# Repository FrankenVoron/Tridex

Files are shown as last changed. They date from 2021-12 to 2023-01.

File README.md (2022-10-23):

# Tridex

Screen_Shot_2022-10-16_at_11 43 59_AM

## Overview

The primary purpose of this IDEX (Independent Dual EXtrusion) printer is to enable dual material prints for soluble/removable supports (ie, ABS primary material + HIPS support material). Other methods of printing dual materials within a single toolhead (such as using a Y splitter, MMU, Palette, etc) have issues due to mixing/contamination within the nozzle which may cause poor layer adhesion. As well, these methods require fairly substantial purge blocks, which generally can be avoided with an IDEX design. 

If you need to prototype parts that have complex geometries (ie, prototyping parts that will be injection molded for mass production), this may be the printer for you! However, if you are designing parts with the final goal of being 3d printed, optimizing the design to be printed without supports will be more reliable, less expensive, and faster overall.

While this printer *may* eventually be "release worthy" with supporting documentation, please note **this is an advanced DIY 3d printer build.** This should not be your first DIY 3d printer, or your first Klipper 3d printer. There is a substantial amount of firmware configuration, macros, slicer setup, tuning, and calibration needed to get from a physically built printer to reliable multi material printer. 

## Specifications

Build Area: 

- Single Toolhead: 225x250x250mm
- Dual Toolhead: 205x250x250mm
- Mirrored/Duplication: Not currently supported with Klipper

Maximum Acceleration:

- Recommended 2000-4000 mm/s^2

This printer is based on the official Voron Trident release files: https://github.com/VoronDesign/Voron-Trident/releases

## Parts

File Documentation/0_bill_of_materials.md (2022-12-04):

# Tridex Bill of Materials

Items in **bold** are new items vs. a stock Trident build

Complete BOM in Progress (with Cost Delta): https://docs.google.com/spreadsheets/d/1dpyxq9-LeO-x1Jcv-8NuVuj9S6S3OHPWxxA0LcGV7Z0/edit?usp=sharing

Frame Calculator: https://docs.google.com/spreadsheets/d/1rIzYha_TP3Gi2qXVKMOwO2kwf7lOrjJWvsjmtj-F2lc/edit?usp=sharing

## Core Items:

- Trident Kit (250x250mm)
- Frame Extrusions:
  - 4 HFSB5-2020-500-LCP-RCP-AV360
  - **3 HFSB5-2020-470-TPW**
  - **1 HFSB5-2020-470-AH235-TPW**
  - **1 HFSB5-2020-470-AH235**
  - **1 HFSB5-2020-430**
  - 6 HFSB5-2020-370-TPW
  - **1 HFSB5-2020-340**
  - 1 HFSB5-2020-330-LTP
  - 1 HFSB5-2020-232-LTP
  - **2 DIN Rails (35mm W) - 470mm**
- **Stealthburner Kit (for 2nd toolhead)**
- **MGN12H 400mm with 2 MGN12H Carriages**
- **2 CAN Toolhead boards with CAN interface**
- **7+ Driver capable control board**
- **4 new Gates 2GT Belts**
  - **Y belt length = ~800mm * 2 belts**
  - **X belt length = ~1900mm * 2 belts**

## Front Idlers:

- **4 M5x50mm SHCS** 
- **2 M5x16 BHCS**
- 6 M5x10 BHCS
- 8 M5 2020 T-Nut
- **4 M5 Hexnut**
- 4 M5 Washer/Shims
- 2 M3x40 SHCS
- **2 M3x30 SHCS**
- 4 M3 Heatset Inserts
- 4 F695 Bearings
- **2 2GT 20T Toothed Idler Pulley (Gates or Generic)**

## XY Joints:

- 8 M5x40 SHCS
- 6 M5 Hexnuts
- 4 M5 Washers/Shims
- 4 M5 2020 T-Nut
- 4 F695 Bearings
- 2 2GT 20T Toothed Idler Pulley (Gates or Generic)
- **10 M3x20 SHCS**
- 4 M3x16 SHCS
- **2 M3 2020 T-Nut**
- **4 M3 Heatset Inserts**
- **High Temp Silicone Wiper**

## Drive Modules

- **4 NEMA14 Stepper Motors (V0.1 Style) - Options:**
  - LDO-35STH52-1504AH(VRN)
  - OMC 14HS20-1504S
  - LDO 35STH48-1684AH(VRN) 
  - (Ideally longer wiring harnesses than V0.1 to reach the bottom of the printer)
- 4 M5x30 BHCS
- **4 M5x16 BHCS**
- 14 M5x10 BHCS
- 16 M5 2020 T-Nuts
- 12 M5 Shims
- 12 F695 Bearings
- 8 M3x30 SHCS
- **6 M3x20 SHCS**
- **4 2GT 20T Pulleys (5mm Bore)**
- **2 Omron Microswitches**
- **4 M2x10 Self Tapping Screws**

## Panels

- Top/Back/Deck/Electronics/Door panels are widened by 100mm

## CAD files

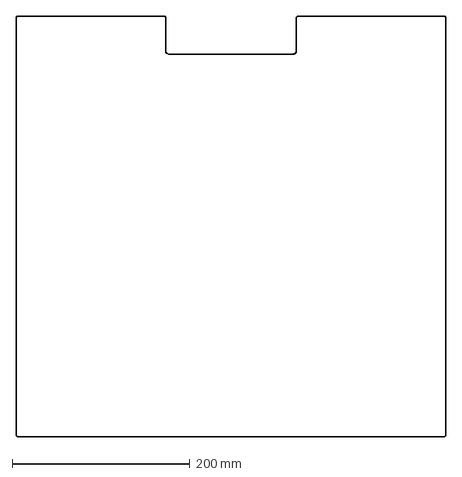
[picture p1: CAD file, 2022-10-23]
Drawings_DXF/350x250_rear.dxf
483.0 x 473.0 mm

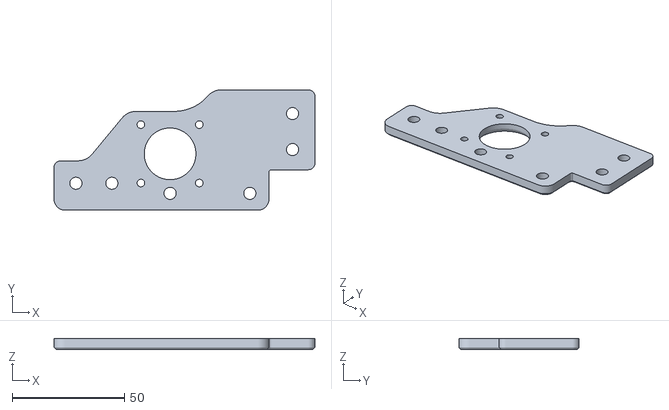
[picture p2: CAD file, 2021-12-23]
Gantry/AB_Drives/a_drive_frame_upper.stl
116.2 x 53.6 x 5.00

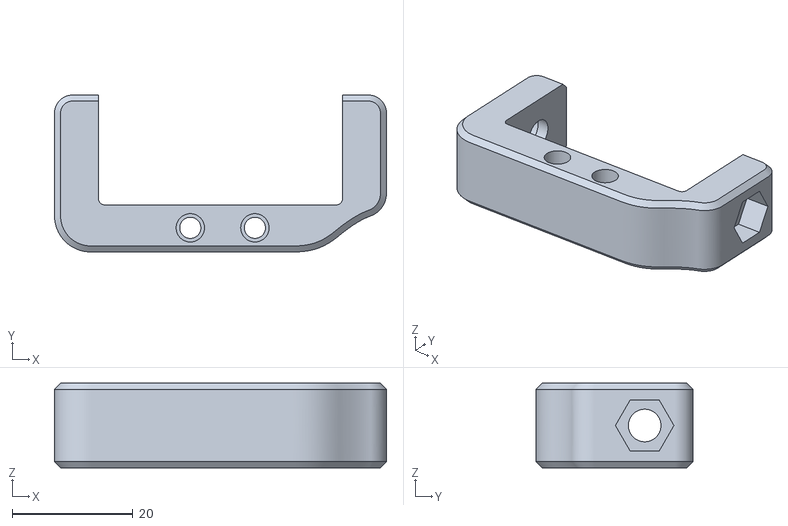
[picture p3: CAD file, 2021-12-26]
Gantry/Front_Idlers/Y_Left_tensioner_Stealth.stl
55.0 x 26.0 x 14.0

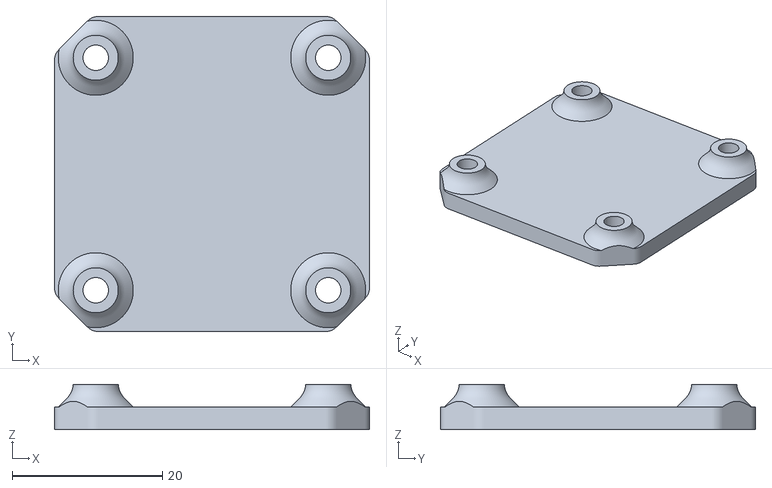
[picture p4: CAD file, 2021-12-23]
Gantry/X_Axis/Huvud_Mount_NEMA17.stl
42.0 x 42.0 x 6.00

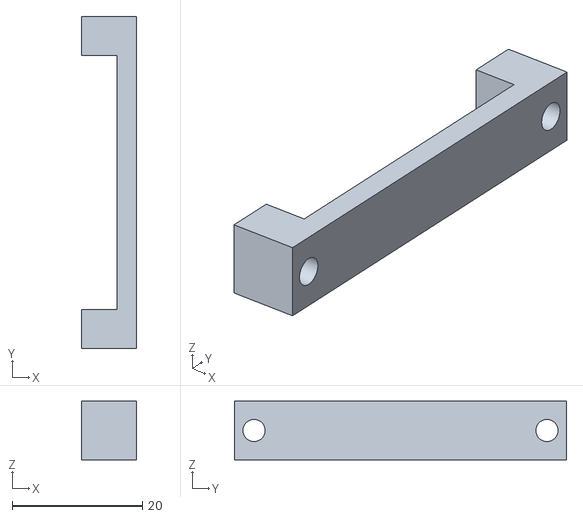
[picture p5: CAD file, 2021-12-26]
Gantry/X_Axis/Nozzle_Scrubber/Left_Brush_Clamp.stl
8.50 x 51.0 x 9.00

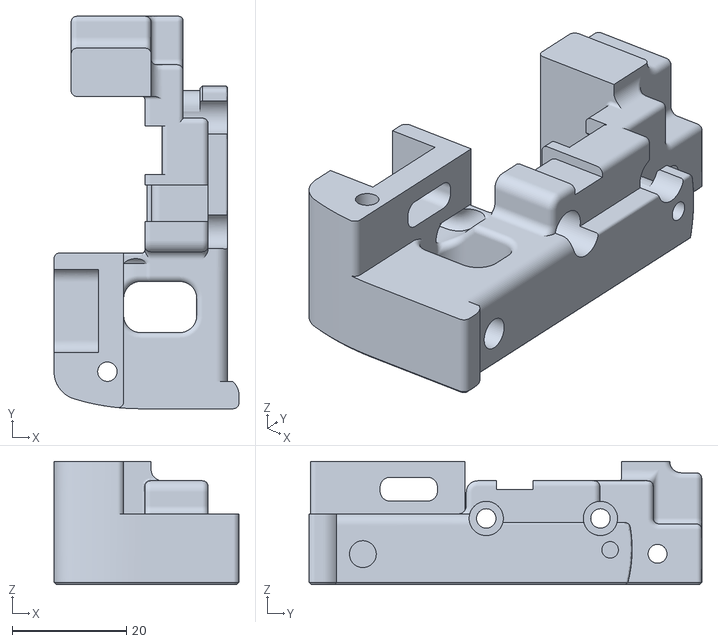
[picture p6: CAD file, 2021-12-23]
Gantry/X_Axis/X_Carriage/CW1 Version/x_carriage_frame_lower_right.stl
32.4 x 68.8 x 21.6

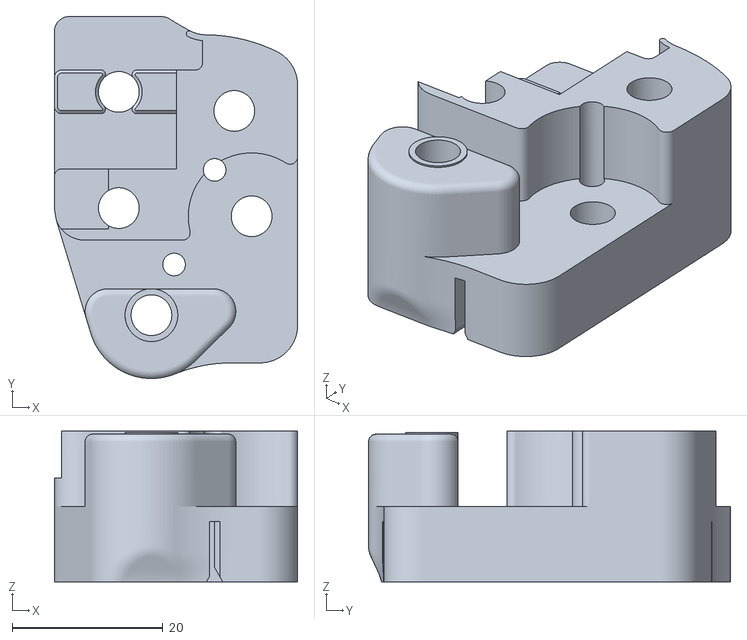
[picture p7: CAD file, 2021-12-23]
Gantry/X_Axis/XY_Joints/xy_joint_right_middle_MGN12.stl
32.3 x 48.0 x 20.0

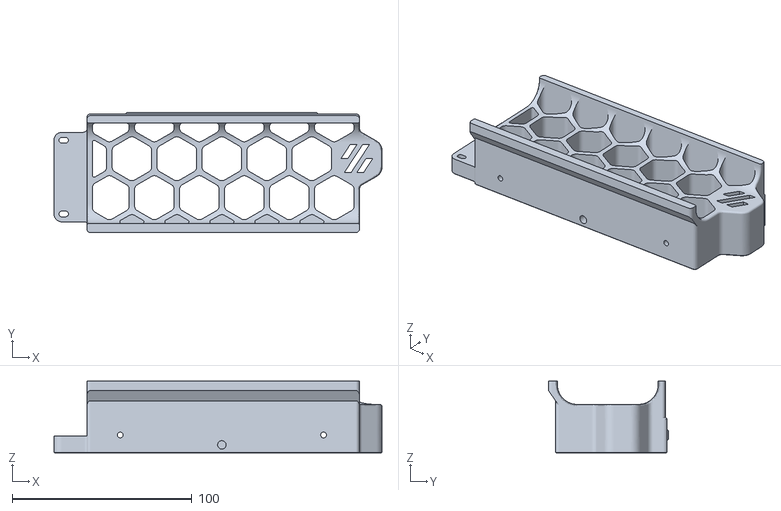
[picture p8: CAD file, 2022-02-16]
Skirts/front_skirt_a_350_deep.stl
182.3 x 66.8 x 40.0

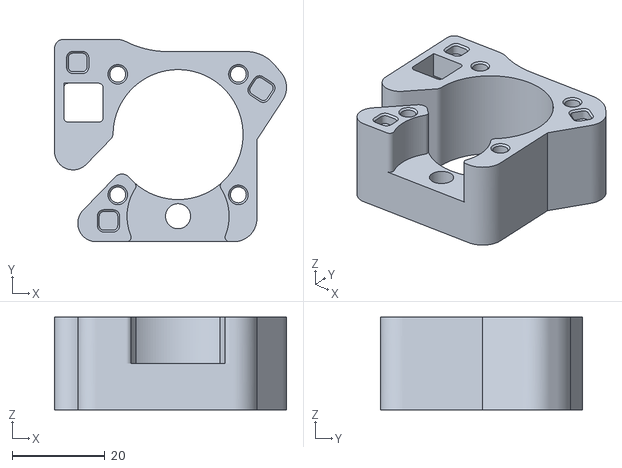
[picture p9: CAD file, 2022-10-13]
STLs/drive_modules/[a]_left_drive_mid.stl
50.0 x 43.7 x 20.0

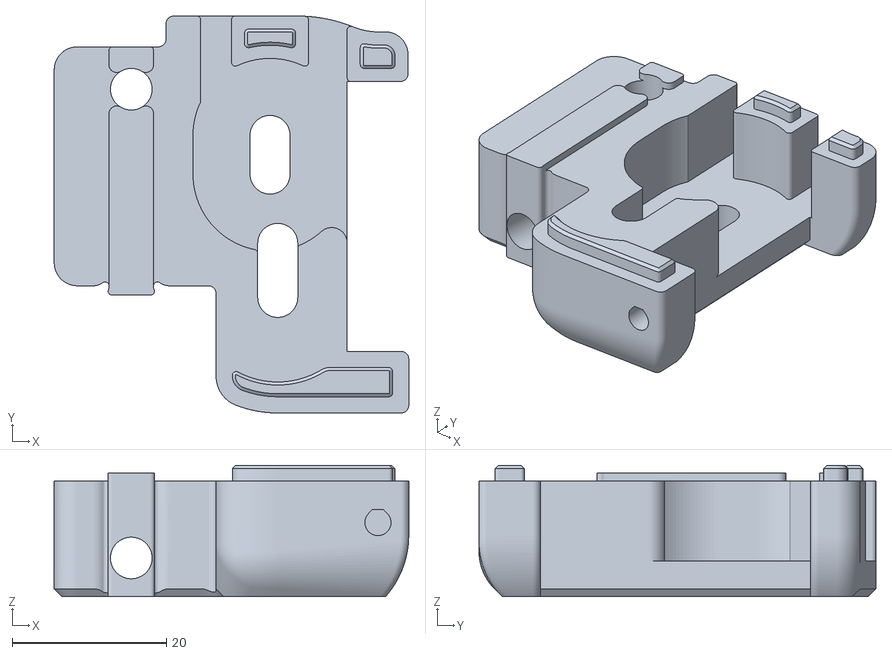
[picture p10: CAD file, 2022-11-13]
STLs/front_idler/idler_front_left_bottom.stl
46.0 x 51.5 x 17.0

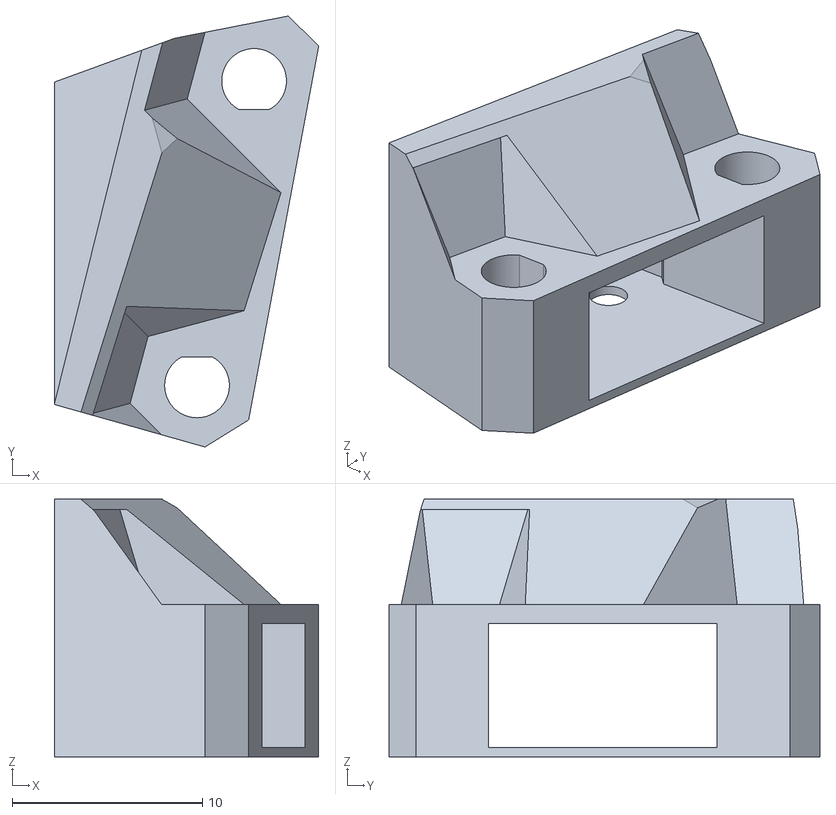
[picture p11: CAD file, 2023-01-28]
STLs/toolhead/Tridex_X_endstop.stl
13.9 x 22.6 x 13.5

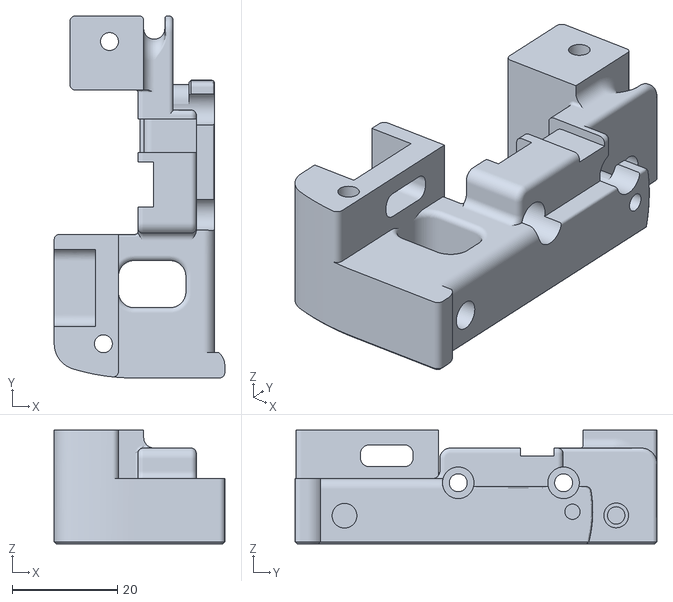
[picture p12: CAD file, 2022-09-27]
STLs/x_carriage_cw2/t0_x_carriage_frame_right.stl
32.4 x 68.8 x 21.6

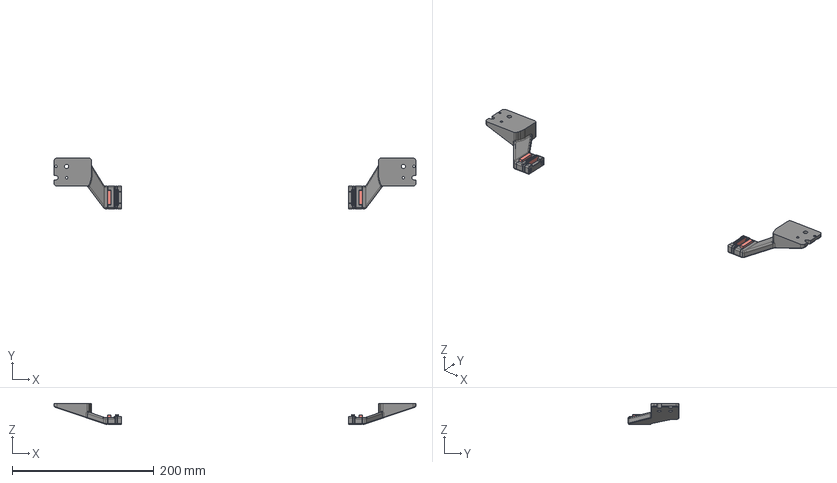
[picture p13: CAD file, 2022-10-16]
STLs/xy_joints/Tridex_XY_RC_Brush_Blocky v4.step
510.6 x 71.4 x 30.2 mm
M3x20 SHCS_91290A123 v1 x 4

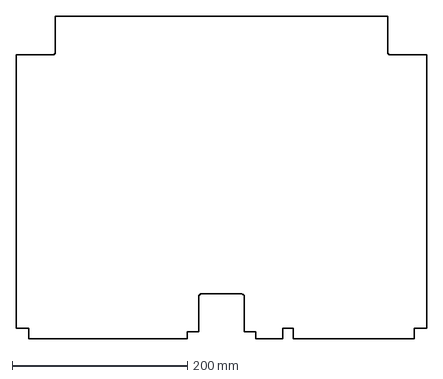
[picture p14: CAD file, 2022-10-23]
Drawings_DXF/350x250_deck.dxf
469.0 x 369.0 mm

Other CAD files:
Gantry/AB_Drives/a_y_motor.stl
Gantry/Front_Idlers/Y_Right_tensioner_Stealth.stl
Gantry/X_Axis/Nozzle_Scrubber/Right_Brush_Mount.stl
Gantry/X_Axis/X_Carriage/CW1 Version/x_carriage_frame_upper_left.stl
CAD/TrideX_Assembly_NozzleBrush v12.f3d
Drawings_DXF/350x250_bottom.dxf
Gantry/AB_Drives/[a]_a_drive_middle.stl
Gantry/AB_Drives/[a]_b_drive_middle.stl
Gantry/AB_Drives/a_drive_frame_lower.stl
Gantry/AB_Drives/b_drive_frame_lower.stl
Gantry/AB_Drives/b_drive_frame_upper.stl
Gantry/AB_Drives/b_y_motor.stl
Gantry/Front_Idlers/A_Tensioner_Stealth.stl
Gantry/Front_Idlers/B_Tensioner_Stealth.stl
Gantry/Front_Idlers/[a]_a_Tensioner.stl
Gantry/Front_Idlers/[a]_b_Tensioner.stl
Gantry/Front_Idlers/[a]_y_left_tensioner.stl
Gantry/Front_Idlers/[a]_y_right_tensioner.stl
Gantry/Front_Idlers/front_idler_a_lower.stl
Gantry/Front_Idlers/front_idler_a_middle.stl
Gantry/Front_Idlers/front_idler_a_upper.stl
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

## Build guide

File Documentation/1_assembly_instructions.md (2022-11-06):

# Assembly Guide for Tridex Gantry

This guide is meant to be a supplement to the standard Voron Trident and Voron Stealthburner/CW2 assembly manuals. It is not official, or final, but hopefully it will help you figure out the order of operations and make life a little bit simpler!

## Part 1: Basic Assembly

Follow the Trident manual, skipping the Front Idler, A/B Drive, and X Axis assembly. You may mount the entire Z assembly including the deck panel, bed, and electronics, and remake the CW2 and Stealthburner fan assemblies per the Stealthburner manual. Mount the Y MGN9 rails to the Y extrusions, but leave the screws loose so that they can slide slightly back and forth.

## Part 2: Drive Modules

Follow PDF instructions in this folder for drive module assembly. Once they are completed, install each drive module onto the gantry extrusions with M5x16 BHCS and M5x10 BHCS.

Fusion360_jOAN20uSyg

## Part 3: Front Idlers

Follow PDF instructions in this folder for front idler assembly. Once they are completed, install each front idler onto the gantry extrusions using M5x16 BHCS and M5x10 BHCS.

Fusion360_WQIAOHZXhy

After securing the front idlers and drive modules, install/slide the MGN9 Y rails backwards until they contact the drive modules. Use the MGN9 3d printed alignment tools to make sure the rail is centered, and secure the rail to the 2020 extrusion.

Fusion360_HXndMWOubw

There will be a gap on the front idlers. This is to allow variation in MGN9 length as well as make it easier to install/remove the drive modules/front idlers if needed in the future without completely removing the MGN9 rail. 

Fusion360_wkdUuxeDLE

## Part 4: XY Joints/Y Belts

Unlike standard Voron Trident XY joint assemblies, the Tridex XY joints must be assembled on the printer in stages. Mount the XY joint lowers to the MGN9 Y rails:

Fusion360_Avvm7I7o4f

Then, take a length of GT2 belt and feed it through the back of the front idler, loop around a GT2 idler, and then feed it through the other opening in the front idler:

Fusion360_W7kKqY3unr

Gently pull the belt out the back of the front idler. This will pull the GT2 idler into place.

Fusion360_r93V2uPN1i

Temporarily insert a M5x50 SHCS through the front idler (without the tensioner arm in place) to hold the GT2 pulley

Fusion360_IgsPVKHUWK

Take the belt closest to the 2020 Y extrusion, and feed it into the rear drive module. If you combine pressure and turning the GT2 pulley by hand, the belt will naturally follow the 3d printed surface and come out the other side. Make sure that belt is not twisted from the front toothed pulley all the way to the Y motor toothed pulley.

Fusion360_UmFg2cfLE5

Flip the left XY joint mid piece over so that you can see the toothed grooves 3d printed into the part.
Fusion360_vsk3gHWyFN
Fusion360_hWV8ZlinC8

For the "free" end of your GT2 belt, make sure it's trimmed cleanly at a 90 degree angle. Insert it into the part so that it overlaps the hole in the belt path. This hole is placed here so that you can push a small screwdriver or hex/allen key through it and push the belt out of the printed channel. 

Fusion360_kDndSNLoMT

With the long end of your GT2 belt, pull it tight and try to remove any obvious slack in the system. **Make sure that your front Y toothed pulley has the M5x50 SHCS through it to hold it into place, or you will cut your belt too short at this step!!**. Cut your belt so that it fits in the other slot in the printed part, similar to the red line in the image above. 

Flip the 3d printed part over, and snap it into the XY Joint Lower piece:

Fusion360_Hjc4LBXLTz

Make sure that the belts are oriented as follows. The "free" end of the Y belt will slide in a channel between the MGN9 carriage and the XY joint.

Fusion360_xVrUfiISvt

Manually pull the M5x50 SHCS screw forward in the Front Idler, and make sure the Y belt can be tensioned without too much front idler movement. If there is a lot of slack in the belt, consider trimming the belt one tooth shorter at a time until there's not much extra slack. As a tip--you can remove the M5x50 SHCS while installing the belt into the toothed slot to make it easier.

Once you are confident with the Y belt length, remove the Y belt, cut another Y belt of identical length, and then install both Y belts in the system. **Do not fully install the Y tensioner yet--just keep the M5x50 SHCS holding the GT2 idler**.

## Part 5: X Axis

Install the X axis MGN12 rail onto the 2020 extrusion. Install Tnuts as needed (2 M5 per side on top, 1 M3 per side on bottom) and screw the X axis to the partially assembled XY joint using a M3x20 from the bottom of the XY joint:

Fusion360_LfYs2FOs7U

Insert a M5x40 SHCS with washer/bearing/bearing/washer into the left XY joint:
Fusion360_kSubw5IJT0

Then install the XY joint upper on top. Insert the additional M5x40 SHCS, hexnuts, and GT2 20T idler:

Fusion360_KyqO03vBuD

On the right XY joint, install the XY joint upper with M5x40, washer/bearing/bearing/washer onto the lower/mid XY joint parts. Install the rest of the M5x40 screws, as well as the GT2 20T idler. 

Fusion360_0UUWuQsBGq

## Part 6: X Belts

In preparation for the X belts, install heatset inserts into the X carriages, and install the T0 X endstop into the left carriage. Do not install bolts through the X carriage yet--it is easier to install the belts with the X carriages as two separate halves.

Route an initial X belt by inserting the ends of the belts into the opening above the X pulley, fishing through the slots in the back of the drive module. 

Fusion360_TNfg9VQteW
Fusion360_Z8PnJcnRFt

The X belt routing is similar to a standard CoreXY belt routing, except upper belt attaches to the left X carriage (T1), and the lower belt attaches to the right X carriage (T1). 
Fusion360_s94B1QZMBw

Since the front tensioner Y accent pieces are not installed, it should be easier to route the X belts through the tensioner body. 

Fusion360_Zz1pREp1Aq

Once the belt is routed, temporarily install an X carriage and pull the X axis flush to the front of the printer, to make sure there is enough belt length. You can leave an inch or two extra belt sticking out of the X carriage if needed

Cut the X belt, and then remove, and cut another X belt exactly the same length. Install both belts, making sure that both have the same amount of extra belt length extending from the X carriages. With this complete, install the M3x30 bolts through the X carriages to make sure both halves are fully secured. 

Remove the M5x50 SHCS from the front Y idler pulleys, and finally install the Y tensioners and tensioning screws
Fusion360_ggaEBeqQwN

If you have difficulty aligning the 20T toothed idler with the M5x50 screw, use an allen key or small screwdriver to push it backwards from the bottom while you insert the M5x50 back in from the top.

## Part 7: Tensioning and Alignment

With all belts installed, double check all belt routing to make sure belts are fully seated on their bearings/pulleys. 

Push the X axis backwards so it's about 3/4 of the way to the back of the printer. Pluck the Y belts (between the XY joints and front idlers) and tension them until there is a clear low bass tone, even on both sides. My printer is currently around 60Hz at about Y=200mm, but this is not scientific. Pluck the X belts and tension them so they match the same tone. Push the X axis backwards and check to see if both Y endstops trigger at the same time--if they do not, slightly tweak the X belt tension until they do. If they don't reliably trigger, install the "Y Endstop Bumpers" (not yet designed) to improve Y endstop performance. 

Check all belt tensions again once both Y endstops are triggering at the same time. If the belt tensions are significantly different between X1/X2, loosen the screws connecting the X axis extrusion to the XY joints, recheck Y endstop triggering/belts, and once belt tension is the same across all belts and the Y endstops trigger at the same time, tighten the X axis 2020/XY joints for a final time. Check all structural bolts through the gantry to make sure they are moderately tight. DO NOT OVERTIGHTEN, just snug: M5x30 BHCS on Drive Modules (idler pulley axles), M5x40 SHCS holding idler pulleys on XY joints, M5x50 SHCS on Front Idler tensioners.

Later on, recheck belt tensions once the printer has homed XY and stepper motors are engaged.

## Part 8: Nozzle Wiper Assembly

Take the nozzle wiper components and insert two heatsets into the ends of each nozzle wiper body. Cut pieces of silicone wiper (based on template) and insert into the slots. Secure silicone pieces with M3x20 SHCS to the end of the wiper body. To mount the wiper assembly to the bottom of the XY joint, note that two of the XY Joint Lower to MGN9 Y rail screws have passthroughs in the nozzle wiper body, and two will be used to mount. Remove the two M3x16 SHCS screws (diagonally) where the nozzle wiper will mount to the XY Joint Lower, and put M3x20 SHCS through the nozzle wiper body, thorugh the XY Joint Lower, and into the MGN9 carriage. Tighten securely, and repeat with both sides.

## Part 9: Toolhead Assembly

Assemble two CW2 modules per the standard CW2 instructions. Mount your choice of CAN control board to the back/sides based on the model. NEMA14 sized CAN boards can be mounted with M3 brass standoffs off the NEMA14 motor, HUVUDs/NEMA17 can be mounted with an arm that replaces the cable chain mount. Stealthburner style CAN boards can be installed integrated into the body of the Stealthburner/CW2. 

For the T0 toolhead (left), print the specific toolhead_rear component in the Tridex repo along with the standard toolhead_front from the stealthburner repo. This modified toolhead_rear has a bumper extension that will allow T1 to home off of it. Note--this toolhead_rear part requires supports at this time. 



For the T1 toolhead (right), print the standard toolhead_front and toolhead_rear from the Stealthburner repo, along with the custom X endstop mount from the Tridex repo. Mount a microswitch with lever into the X endstop mount, with wire leads extending through the toolhead_rear mount behind the hotend heatsink, where the wires will join the rest of the hotend thermistor/heater wires to travel up to CW2. 



Mount the X endstop mount to the toolhead body with M3 screws into the heatset inserts in the toolhead body.







Assemble the Stealthburner fan assembly per the standard instructions. Double check the X carriage is sitting flush/properly with the MGN12H rail and all screws are tight--if it is not, it will create large offsets between the toolheads. Mount the CW2, Toolhead, and Stealthburner onto the X carriage, and tighten securely. Make sure any extra 2GT belt does not get pinched between the toolhead body and the X carriage, since this will create large offsets.

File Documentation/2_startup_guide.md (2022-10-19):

# Initial Startup Guide

This guide is heavily inspired by Klipper's Configuration Check guide: https://www.klipper3d.org/Config_checks.html

## 1. Klipper Setup

Flash MainsailOS or FluiddPi to your Raspberry Pi micro SD card, and configure your microcontroller and CAN interfaces. There are a variety of different resources available that may be helpful, but it is expected that you will be comfortable flashing/configuring the device that you choose!

- [MainsailOS](https://github.com/mainsail-crew/MainsailOS/tags)
- [FluiddPi](https://github.com/fluidd-core/FluiddPI/tags)
- [Klipper Mainsail CAN Setup Guide](https://www.youtube.com/watch?v=XkcxSQhRR3I)
- [CanBoot Flashing Guide](https://youtu.be/YrF99Sff9g8)
- [BTT EBB V1.0 CAN Setup Guide](https://youtu.be/_FELCN8CbWA)

## 2. Configuration

### Endstop Checks

Save the firmware configuration files from the Tridex Github to your printer, and edit them to match your control boards and printer specification. Once Klipper starts successfully without throwing errors, verify each of the endstops to make sure they function as expected by manually triggering the endstop with your finger or a tool. The status can be checked in the "Machine" page of Mainsail by refreshing the endstop status section.

- Endstop X (left toolhead X endstop)
- Endstop Dual_Carriage (right toolhead X endstop)
- Endstop Y (left Y endstop)
- Endstop Y1 (right Y endstop)
- Endstop Z (Z nozzle pin)
- Probe (Omron probe or Klicky, etc)

Once each endstop is configured so that it reads `Triggered` when pressed, and `Open` when not pressed, go ahead and push the X axis towards the back of the printer and make sure that both Y endstops trigger off of the X axis. If only one can trigger, tighten or loosen one of the X belt tensioners until both trigger approximately simultaneously. Also, verify that the T0 (left) toolhead X endstop can physically trigger off of the left XY joint, and that the T1 (right) toolhead X endstop can trigger off of the T0 (left) toolhead. 

### Stepper Motors

Next, let's talk about stepper motors checks! Similar to single toolhead Voron printers, the origin (X=0, Y=0) is located at the front left corner of the bed, with positive X traveling to the right, and positive Y movement traveling to the back. For starters, we need to make sure all of the motors are connected to the right connectors and are moving the correct directions. For this, we will use  `STEPPER_BUZZ STEPPER=[stepper name]`. This command will move the stepper back and forth--the first movement after sending the command will be in the "+" axis direction, and then "-". 

- `STEPPER_BUZZ STEPPER=stepper_x` - T0 (left toolhead) should move right (+), then left (-)
- `STEPPER_BUZZ STEPPER=dual_carriage` - T1 (right toolhead) should move right (+) then left (-)
- `STEPPER_BUZZ STEPPER=stepper_y` - left Y motor should move back (+) and then to the front (-)
- `STEPPER_BUZZ STEPPER=stepper_y1` - right Y motor should move back (+) and then front (-)
- `STEPPER_BUZZ STEPPER=stepper_z`- front left Z motor should move down (+) and then up (-)
- `STEPPER_BUZZ STEPPER=stepper_z1`- back Z motor should move down (+) and then up (-)
- `STEPPER_BUZZ STEPPER=stepper_z2`- front right Z motor should move down (+) and then up (-)

### Homing

Next, we need to check the homing sequence. The order of homing is different with a Tridex than with a Trident. An overview of the order is as follows:

1. Home Y to Y=max (back of printer)
2. Home T0 (left toolhead) to X=min (left of printer)
3. Home T1 (right toolhead) to T0 (left of printer)
4. Move T1/Park T1
5. Move T0 to Z endstop pin location
6. Home Z

The default printer configuration file already has homing set up properly for you, however, this configuration file may be updated in the future to be more universal and user friendly. For now, follow these steps **and be sure to have access to the "Emergency Stop" button in Mainsail/Fluidd**:

1. Use macro `IDEX_HOME_Y` (visible on Mainsail dashboard). The printer should move the X axis backwards until both Y endstops are triggered, and then move forward approximately 35mm. **If it moves to the front of the printer at first and doesn't stop, hit the Emergency Stop button! If the Y motors move in opposite directions, hit the Emergency Stop button!** 

If either of these cases occurs--double check your STEPPER_BUZZ commands and invert the direction pin of the stepper motor that is not traveling in the correct direction. Also, double check your `position_endstop`--it should be set equal to position_max. If it is set to something else (like position_min)--the printer will home in the incorrec direction. 

2. Once you have successfully homed Y, use macro `IDEX_HOME_X`. The printer should move the left toolhead (T0, controlled by stepper_x) to the left until it triggers the T0 x endstop, and then it should move the right toolhead (T1, controlled by dual_carriage) to the left until it triggers the T1 x endstop. Then, it should move the T1 toolhead to the right to about the middle of the printer, and then move it to the parked position close to the right of the X axis. T0 should become active at this point, and move to about the center of the printer. **If either toolhead doesn't travel in the correct direction, or crashes, press the Emergency Stop Button immediately!** 

The initial printer.cfg in the Tridex repository should properly define the `position_endstop` for both `stepper_x` and `dual_carriage`, but if you have issues with homing, double check both the `STEPPER_BUZZ` directions and toolheads as well as the position endstop for both. `[stepper_x]` should have a `position_min` and `position_endstop` of approximately -50, and `[dual_carriage]`should have `position_min` and `position_endstop` of approximately 22. 

3. Once both X and Y have homed successfully, (by running `IDEX_HOME_Y` and then `IDEX_HOME_X`), make sure T0 is active (press the T0 button in Mainsail), and move the toolhead using Mainsail until the nozzle is above the Z endstop pin. Record these coordinates (X and Y) and update your [homing_override] section so that the toolhead goes to this point prior to homing Z. (More documentation needs to be added for this step). Your z pin location should be somewhere close to X = 145-150mm and Y = 250-255mm for a standard 250x250mm Tridex build. 
4. Once you have updated your configuration, saved it, and restarted klipper, now is the exciting point! Press the "Home All" button in Mainsail. The printer should home Y, home X, and then move T0 to the Z endstop pin location and home. **Be sure to be ready to press the Emergency Stop button!** 

Even if the nozzle touches the Z endstop pin successfully, double check the location again and make sure that the nozzle is as close to the center of the Z endstop pin as possible. With this final adjustment, save the configuration, restart the printer, and home again!

5. Finally, we need to verify that the probe works as expected! If you are using an inductive probe, make sure that the probe triggers off of a piece of metal and the bed by checking the endstop status. Then, run a Z_TILT_ADJUST (or "Z-TILT" in Mainsail) to level the bed. Finish by running a final G28 to home Z again off of the Z pin. 

Congratulations! You've successfully homed your Tridex printer!

### Heaters and Fans

Follow the standard [Klipper Configuration Checks](https://www.klipper3d.org/Config_checks.html) guide to test each of your hotend fans, hotend heaters, part cooling fans, and bed heater. PID calibrate each heater individually, saving the configuration after each tune.

### Extruder

With your hotend heated, try extruding some filament through each toolhead. If the extruder is going in the wrong direction (retracting instead of feeding filament), invert the direction pin for that given extruder. Press the "T0" or "T1" buttons to switch between toolheads to test each one. Finally, calibrate your extruder by extruding 100mm of filament and verifying that 100mm of filament is fed through the extruder. It is critical that both extruders are functionally extruding the same amount of filament!

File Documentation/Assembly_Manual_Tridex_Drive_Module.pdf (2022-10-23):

Y ENDSTOP MOUNTING | WWW.VORONDESIGN.COM

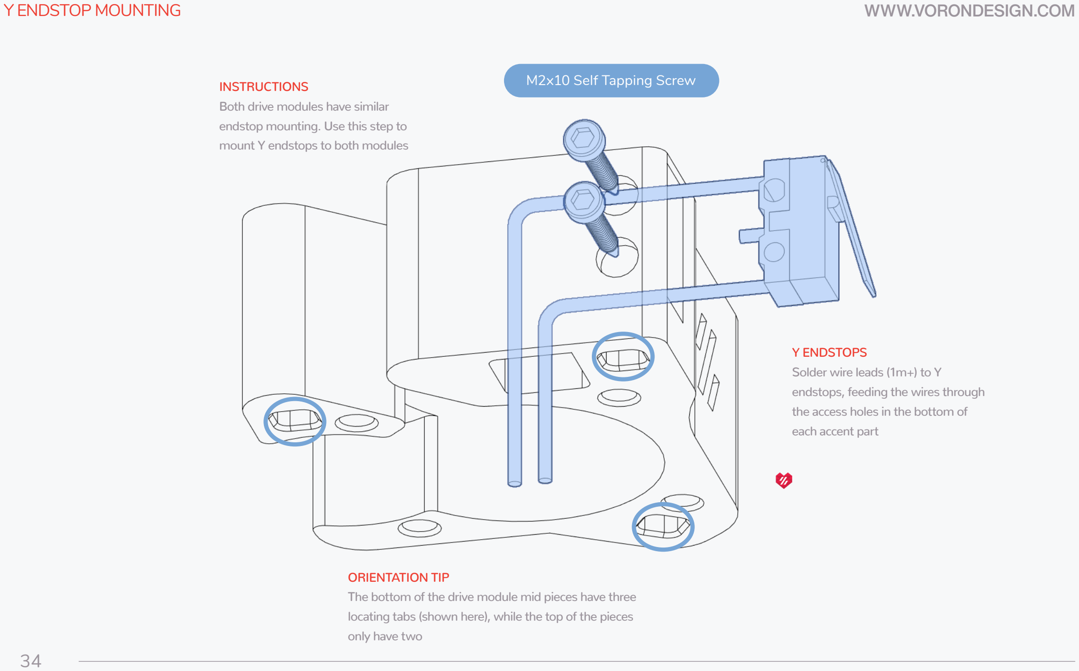
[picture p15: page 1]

34

Y ENDSTOPS
Solder wire leads (1m+) to Y endstops, feeding the wires through the access holes in the bottom of each accent part

INSTRUCTIONS
Both drive modules have similar endstop mounting. Use this step to mount Y endstops to both modules

ORIENTATION TIP
The bottom of the drive module mid pieces have three locating tabs (shown here), while the top of the pieces only have two

M2x10 Self Tapping Screw

LEFT DRIVE MODULE | WWW.VORONDESIGN.COM

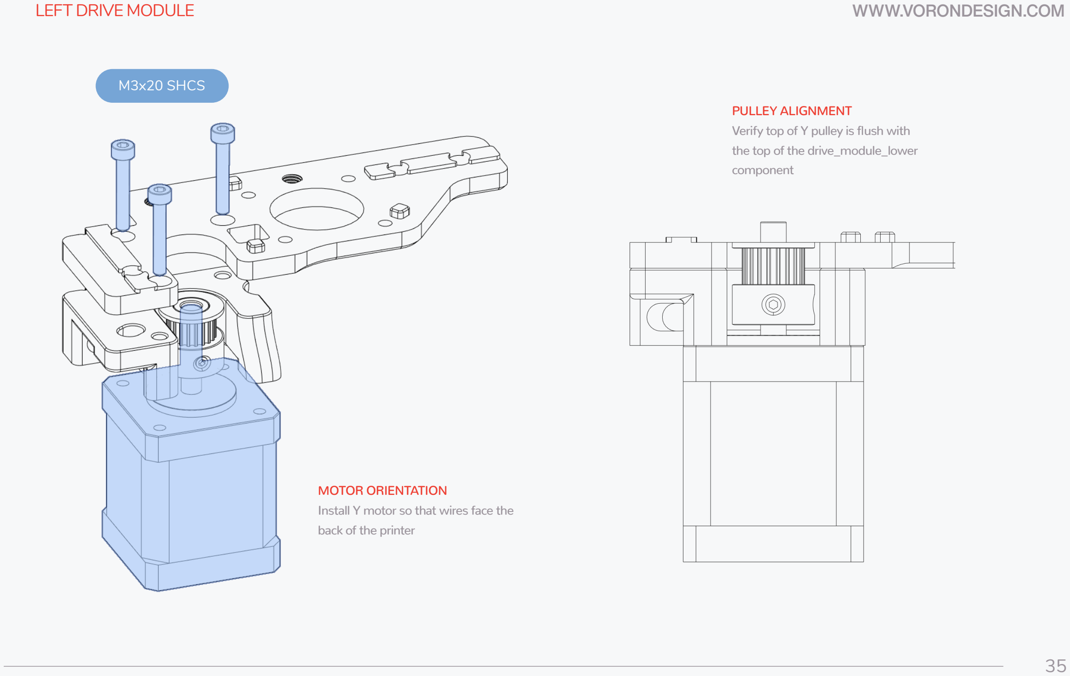
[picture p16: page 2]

35

M3x20 SHCS

MOTOR ORIENTATION
Install Y motor so that wires face the back of the printer

PULLEY ALIGNMENT
Verify top of Y pulley is flush with the top of the drive_module_lower component

### WWW.VORONDESIGN.COM

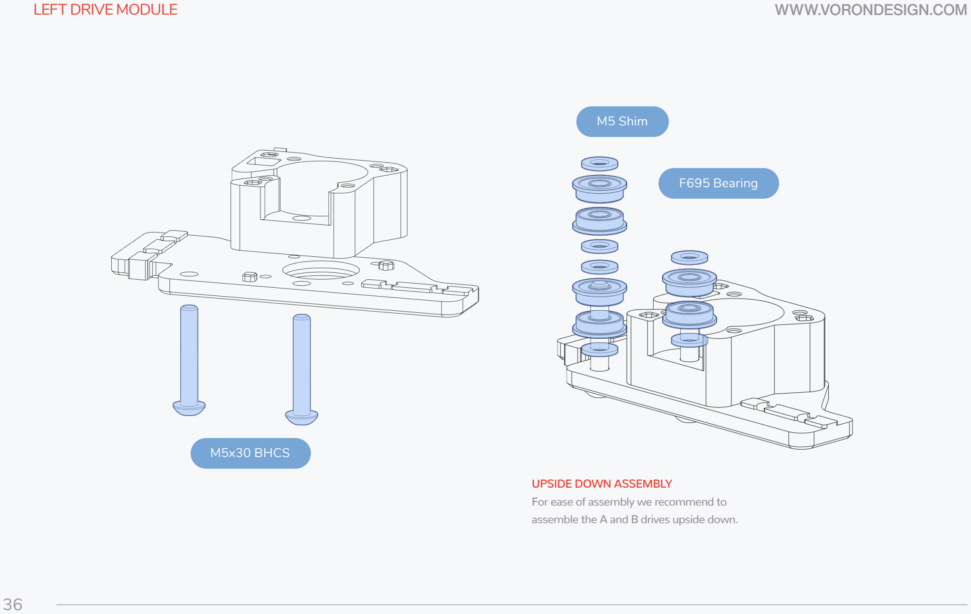
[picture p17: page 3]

36

M5 Shim

F695 Bearing

LEFT DRIVE MODULE

UPSIDE DOWN ASSEMBLY
For ease of assembly we recommend to assemble the A and B drives upside down.

M5x30 BHCS

LEFT DRIVE MODULE | WWW.VORONDESIGN.COM

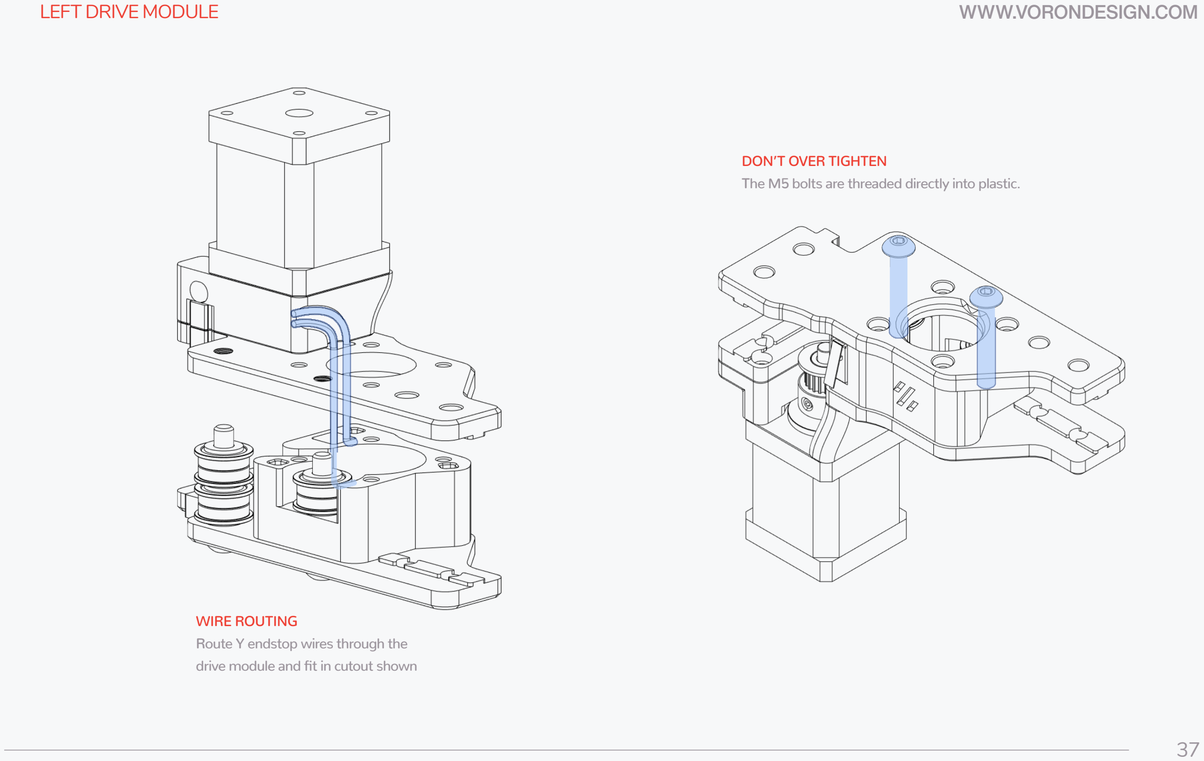
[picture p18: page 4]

37

WIRE ROUTING
Route Y endstop wires through the drive module and fit in cutout shown

DON’T OVER TIGHTEN
The M5 bolts are threaded directly into plastic.

LEFT DRIVE MODULE | WWW.VORONDESIGN.COM

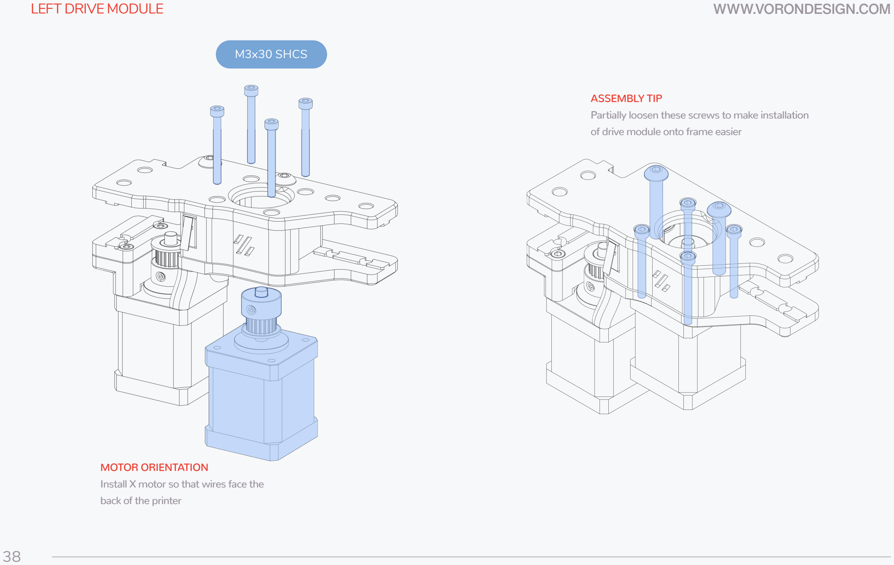
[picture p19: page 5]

38

ASSEMBLY TIP
Partially loosen these screws to make installation of drive module onto frame easier

M3x30 SHCS

MOTOR ORIENTATION
Install X motor so that wires face the back of the printer

RIGHT DRIVE MODULE | WWW.VORONDESIGN.COM

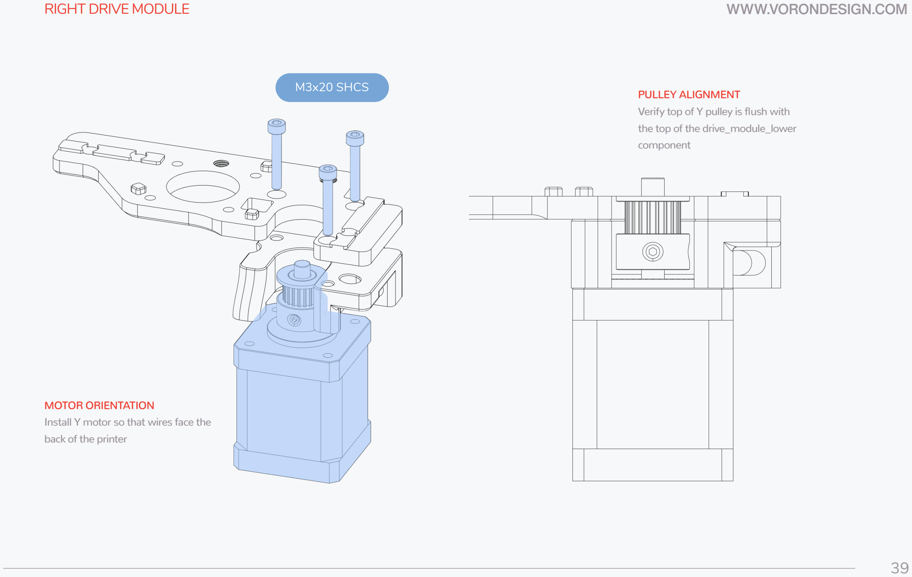
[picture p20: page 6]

39

M3x20 SHCS

MOTOR ORIENTATION
Install Y motor so that wires face the back of the printer

PULLEY ALIGNMENT
Verify top of Y pulley is flush with the top of the drive_module_lower component

RIGHT DRIVE MODULE | WWW.VORONDESIGN.COM

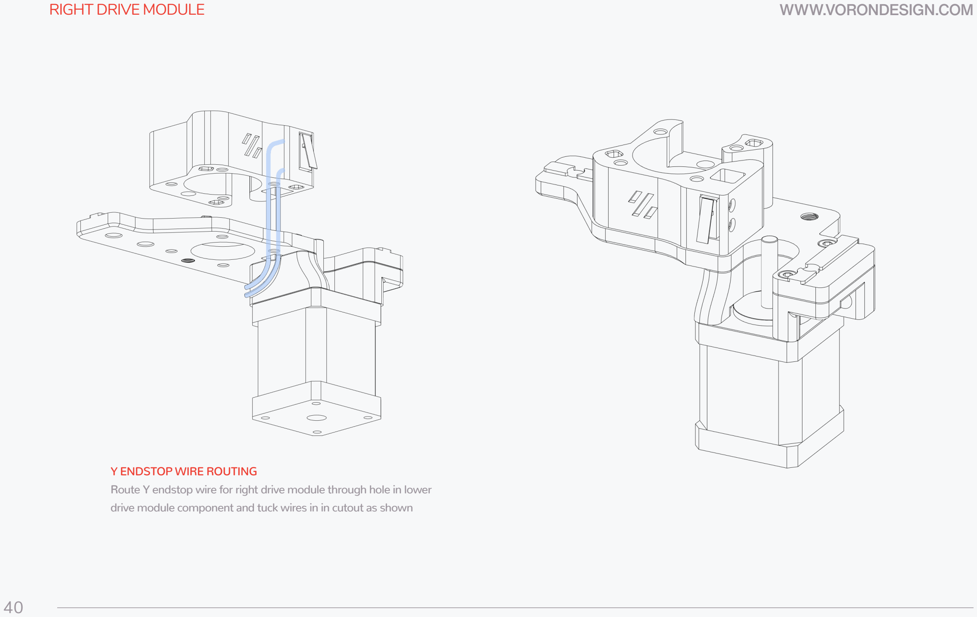
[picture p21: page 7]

40

Y ENDSTOP WIRE ROUTING
Route Y endstop wire for right drive module through hole in lower drive module component and tuck wires in in cutout as shown

### WWW.VORONDESIGN.COM

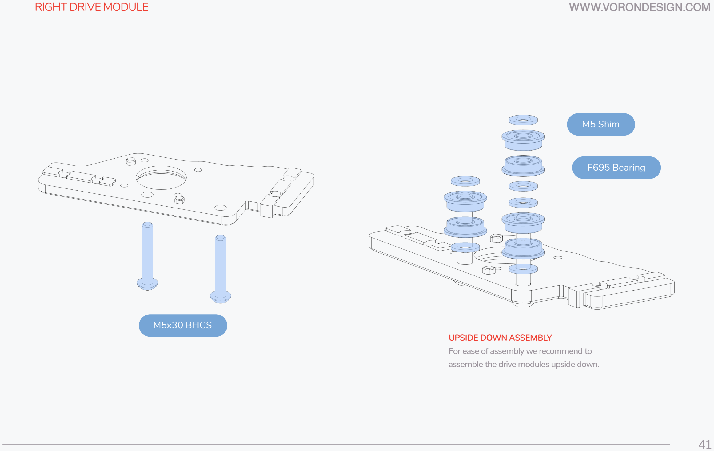
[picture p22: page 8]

41

M5 Shim

F695 Bearing

RIGHT DRIVE MODULE

UPSIDE DOWN ASSEMBLY
For ease of assembly we recommend to assemble the drive modules upside down.

M5x30 BHCS

RIGHT DRIVE MODULE | WWW.VORONDESIGN.COM

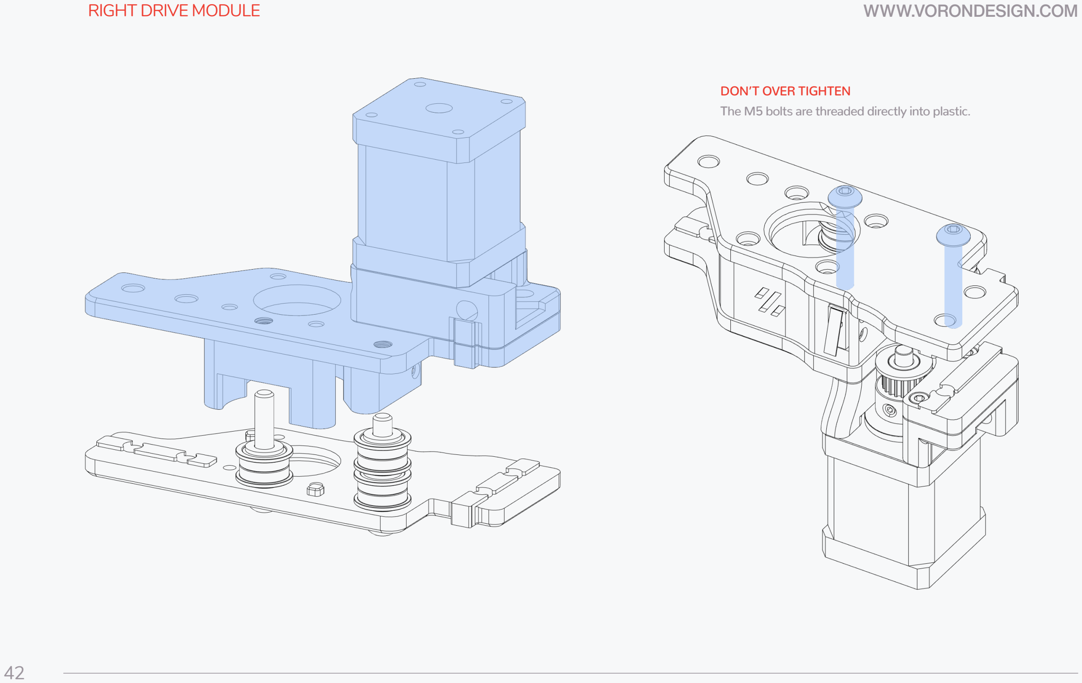
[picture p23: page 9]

42

DON’T OVER TIGHTEN
The M5 bolts are threaded directly into plastic.

RIGHT DRIVE MODULE | WWW.VORONDESIGN.COM

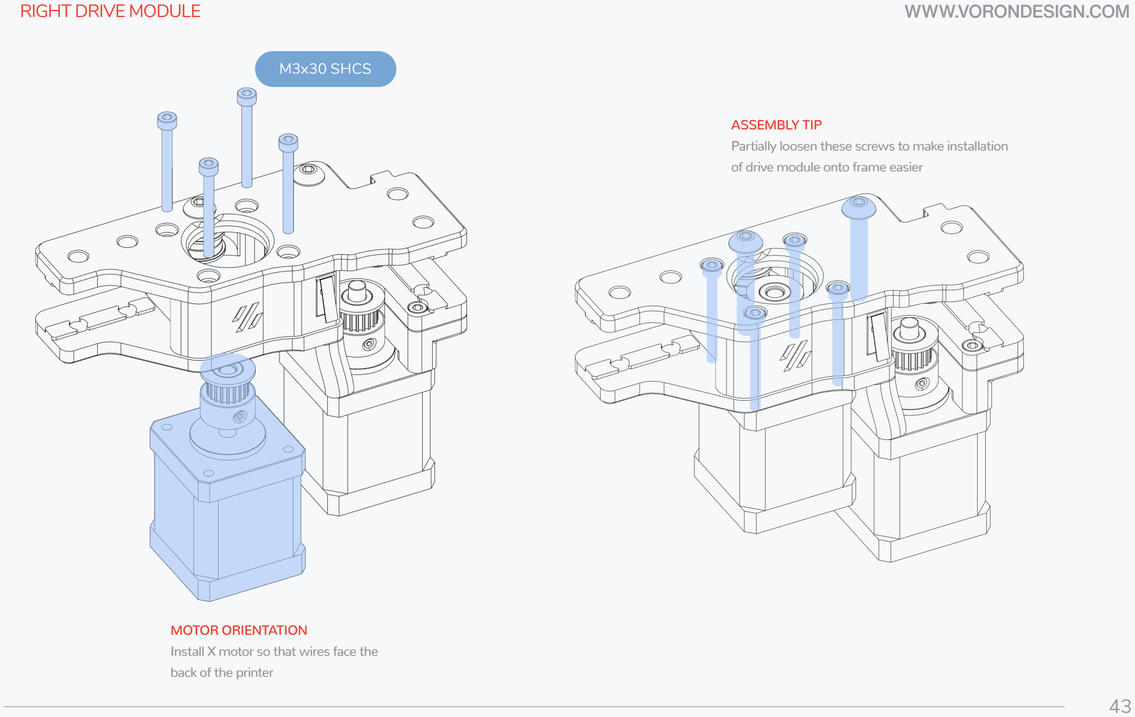
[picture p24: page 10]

43

ASSEMBLY TIP
Partially loosen these screws to make installation of drive module onto frame easier

M3x30 SHCS

MOTOR ORIENTATION
Install X motor so that wires face the back of the printer

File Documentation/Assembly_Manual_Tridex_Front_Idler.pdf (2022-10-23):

COMPONENT PREP | WWW.VORONDESIGN.COM

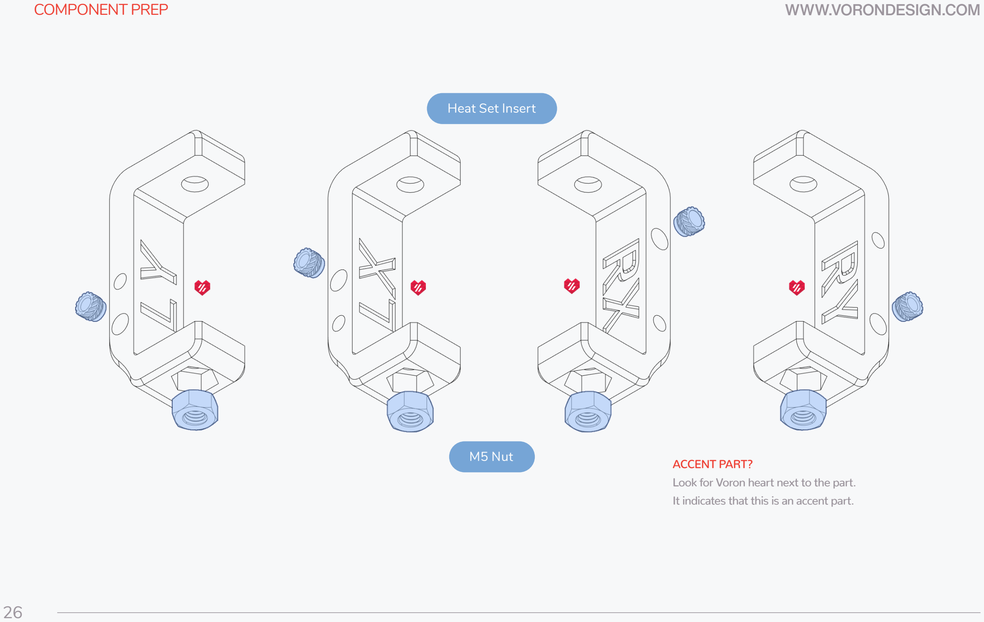
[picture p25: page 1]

26

M5 Nut

Heat Set Insert

ACCENT PART?
Look for Voron heart next to the part. It indicates that this is an accent part.

LEFT IDLER | WWW.VORONDESIGN.COM

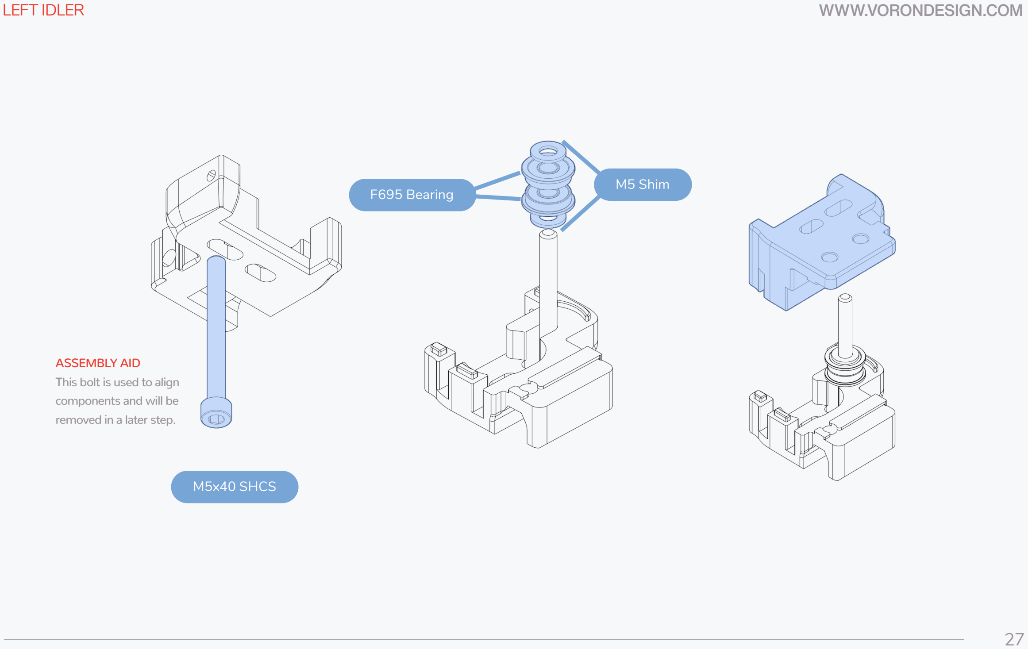
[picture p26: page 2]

27

M5x40 SHCS

M5 Shim
F695 Bearing

ASSEMBLY AID
This bolt is used to align components and will be
removed in a later step.

LEFT IDLER | WWW.VORONDESIGN.COM

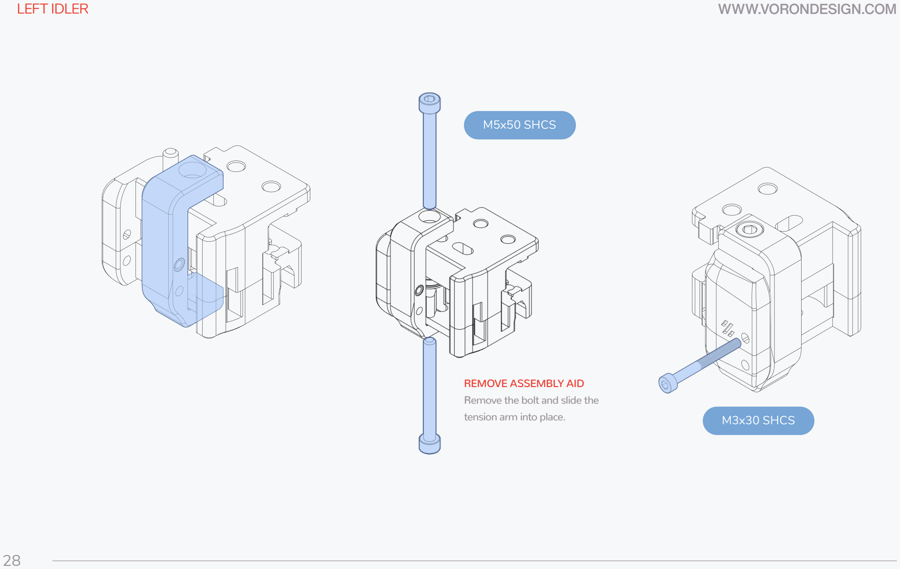
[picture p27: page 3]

28

M5x50 SHCS

M3x30 SHCS

REMOVE ASSEMBLY AID
Remove the bolt and slide the tension arm into place.

RIGHT IDLER | WWW.VORONDESIGN.COM

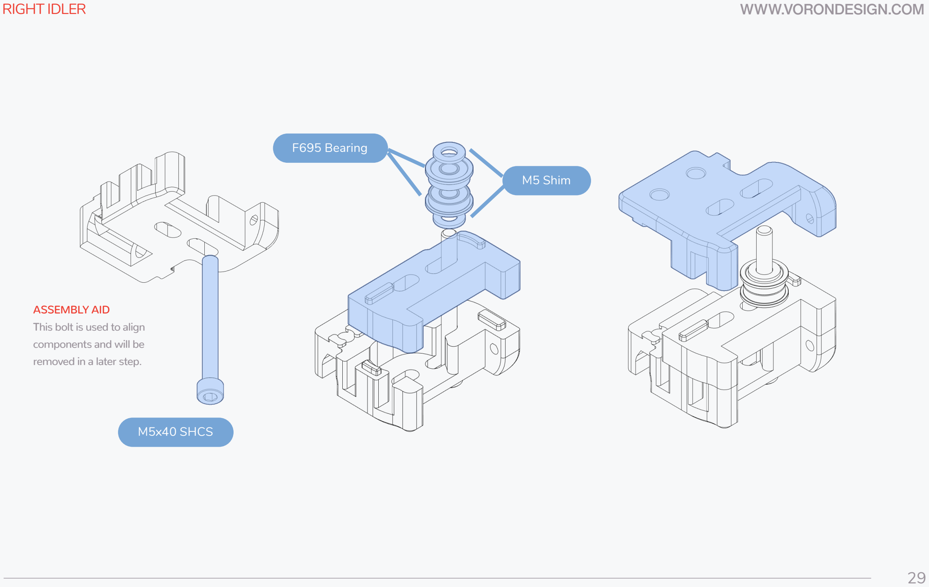
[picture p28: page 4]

29

M5x40 SHCS

M5 Shim

F695 Bearing

ASSEMBLY AID
This bolt is used to align components and will be
removed in a later step.

RIGHT IDLER | WWW.VORONDESIGN.COM

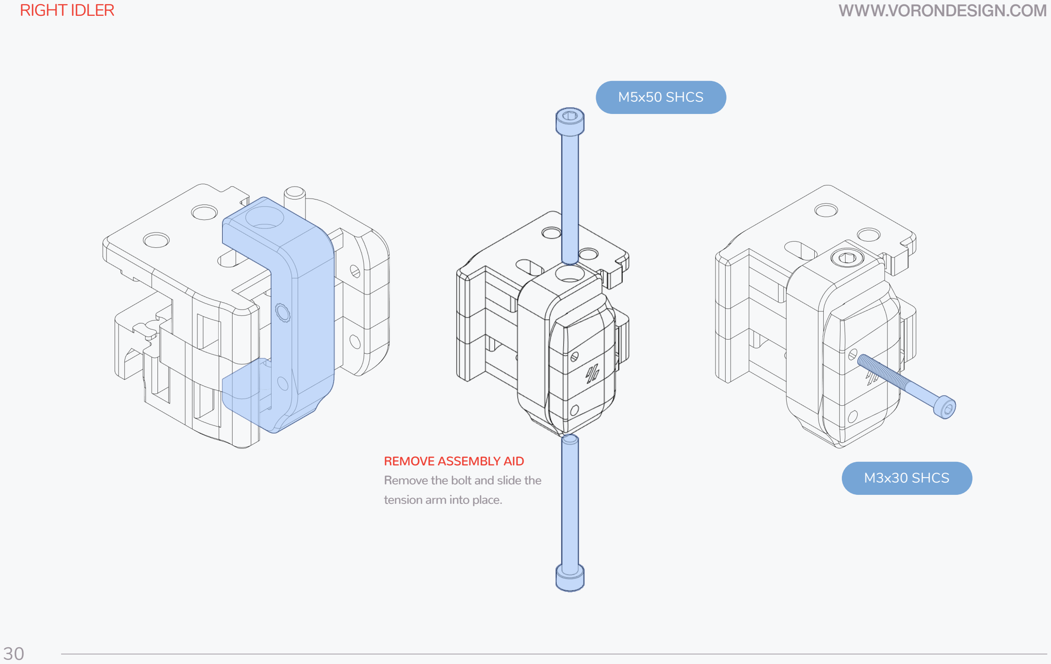
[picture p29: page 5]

30

M5x50 SHCS

M3x30 SHCS

REMOVE ASSEMBLY AID
Remove the bolt and slide the tension arm into place.

FRONT IDLERS | WWW.VORONDESIGN.COM

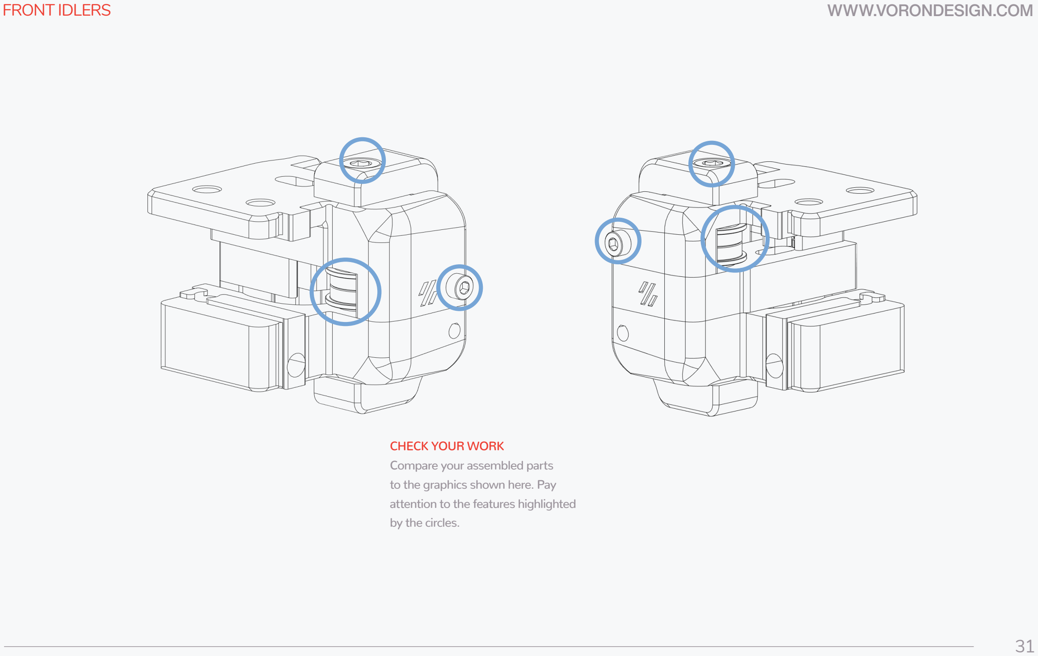
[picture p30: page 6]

31

CHECK YOUR WORK
Compare your assembled parts to the graphics shown here. Pay attention to the features highlighted by the circles.

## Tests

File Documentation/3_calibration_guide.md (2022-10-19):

# Calibration Guide

This guide is a work in progress, and is a collection of different tuning steps that may not be complete or have the supporting configuration parameters. This guide assumes you have followed the previous getting started guide and your printer homes and extrudes filament!

## Rough Offset Calibration

For an IDEX printer, we have 3 offsets that we need to calibrate--X, Y, and Z! Check your IDEX_mode.cfg file and verify that all of your offset variables are set to 0 (variable_offset_x, variable_offset_y, and variable_offset_z). 

First off, it's important that your T0 (left, primary) toolhead is printing well and has a good first layer Z position. Using a hot bed and extruder, move the T0 nozzle to the center of the bed and lower the nozzle until it barely touches a sheet of paper as the paper is moved back and forth. This height should be approximately Z = 0.1mm. Adjust the `[stepper_z]` `position_endstop`, save, restart Klipper, and test until this is true.

Once your T0 nozzle is touching the sheet of paper at 0.1mm, raise the toolhead a few millimeters, switch to T1, and begin lowering the T1 nozzle until it touches the sheet of paper. Record the value--if T1 is touching at 0.17mm and T0 is touching at 0.1mm, the `variable_offset_z` will be T1 - T0 = 0.17 - 0.1 = 0.07mm. Update your IDEX_mode.cfg file and restart Klipper.

Next, let's tune the variable_offset_x! After homing the printer, find an object (such as a block) and place it on the print bed, raise or lower the bed height as necessary so that the nozzle is within a few millimeters of the block. Move the block around until one of the edges is aligned with the center of the T0 nozzle. Record the X position of T0 at this point, then switch to T1, and move the toolhead back and forth in X using the commands in Mainsail until the nozzle is positioned the same as the T0 nozzle was. Record the T1 position, and then calculate the new variable_offset_x as T1_x - T0_x = value. Update your IDEX_mode_cfg file and restart klipper! (Note--if this offset value is very large, you can choose to update the dual_carriage position_endstop instead so that the offset is small)

Finally, tune variable_offset_y. Use the same setup as with X, except adjust the toolheads in Y instead of X! 

These initial calibration values are rough approximate values that will help your printer be in the ballpark. Your Z and Y offsets should be small, generally less than 0.5mm.

## Fine Offset Calibration

It's time for a calibration tuning print! This is a good starter print: [Dual Extruder Calibration Vernier](https://www.thingiverse.com/thing:3873434), Adjust values slightly as needed and reprint until both extruder prints are relatively aligned. 

For a "normal" test print I use [Easter Island Moai - Dual Extrusion Style.](https://www.thingiverse.com/thing:1560492) This is a great print since it allows you to see offsets between the toolheads on the first layer! Adjust offsets as needed, remembering that each offset value is the delta between T0 and T1:

### X Offset Guide

T1 color too far +X (right) => reduce variable_offset_x

T1 color too far -X (left) => increase variable_offset_x

### Y Offset Guide

T1 color too far +Y (back) => reduce variable_offset_y

T1 color too far -Y (front) => increase variable_offset_y

### Z Offset Guide

T1 AND T0 too close to bed => reduce [stepper_z] position_endstop

T1 AND T0 too far from bed => increase [stepper_z] position_endstop

T0 too close to bed, T1 perfect => reduce [stepper_z] position_endstop AND variable_offset_z by same amount

T0 too far from bed, T1 perfect => increase [stepper_z] position_endstop AND variable_offset_z by same amount

T0 perfect, T1 too far from bed => reduce variable_offset_z

T0 perfect, T1 too close to bed => increase variable_offset_z

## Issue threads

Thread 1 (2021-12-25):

Updated CAD Files

Markus-1984, 2021-12-25:
Hi FrankenVoron,

realy nice mod for the Trident. I like Tridex ;-)
Can you please update the CAD Files. I´ve looked into the f3d assembly and only see a few modifications. I would like to see the full assembly before I decide to build it.

Best regards
Markus

eddietheengineer, 2022-01-16:
Check the additional CAD files I updated a few days ago--not in the main assembly, but should show you how the various components have changed!

Closed 2022-01-16.

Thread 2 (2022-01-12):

Extrusions Needed

ExaltedStudios, 2022-01-12:
Removing this to not have anyone go out and get parts when things might change.

eddietheengineer, 2022-10-16:
Added a BOM page to the files with details for frame extrusions!

Closed 2022-10-16.

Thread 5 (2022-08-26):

wrong orientation of [a]_b_drive_middle stl is upside down

ThomasDennisSp, 2022-08-26:
the [a]_b_drive_middle stl is not in the right orientation for easy printing and is upside down so that you have to bridge ca. 2cm but the [a]_a_drive_middle stl is the otherway os you dont have to bridge noticed it because it came lose in printing

eddietheengineer, 2022-10-16:
fixed with latest file release! Thanks

Closed 2022-10-16.

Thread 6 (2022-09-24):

Idler M5 Bolts wrong size in cad model

ThomasDennisSp, 2022-09-24:
in the Cad Modell is the Bolt titled m5x40 but if you messure it it is a m5x50

eddietheengineer, 2022-09-27:
Thank you for pointing this out! I forgot about that!

eddietheengineer, 2022-10-16:
Fixed with the latest CAD :)

Closed 2022-10-16.

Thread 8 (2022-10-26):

sb_dragon_rear_tridex.stl wrong orientation

ThomasDennisSp, 2022-10-26:
title

eddietheengineer, 2023-01-28:
Fixed!

Closed 2023-01-28.

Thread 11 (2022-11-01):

spacer x pulley as qol feature

ThomasDennisSp, 2022-11-01:
Having a spacer for the x motorpulley position on the shaft or a distance so it isnt such a hassle in the assembly whould be a great QOL feature for the future

eddietheengineer, 2023-01-28:
@ThomasDennisSp would something like a pulley alignment jig help? I think I can make one of those fairly quickly

ThomasDennisSp, 2023-01-28:
i think something like the pulley jig what you have in the trident and 2.4 files which is a spacer to get the position right whould be handy to have

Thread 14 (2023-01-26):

How do I use Tridex Frame Calculator

rlarudqls630, 2023-01-26:
Hi, this is a really cool project I was looking for for such a long time.
However, I cannot find a way to use the docs.
What should I put into "edit these cells"?
Trident build volume or frame dimension or something else?

eddietheengineer, 2023-01-28:
@rlarudqls630 I've updated some wording on the calculator--hopefully that is helpful to explain. The "edit these cells" would be the standard "Trident" style frame size, and then in the lower right of the calculator it shows how your X build dimension is impacted.

rlarudqls630, 2023-01-29:
So I need to put the frame dimension right?

eddietheengineer, 2023-01-29:
so, in the edit cells, you would put the Y and Z build area dimensions that you would like. The stock is 250mm Z and 250mm Y.

Then, you'd adjust the X dimension so that the green boxes on the bottom right match the build area (X) that you need.

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

rlarudqls630, 2023-01-30:
So if I want 300X300 build size
I need to change X and Y value and match until Dual Material is 300?
or change Y value to 300 and just adjust X values?

seacred, 2023-05-29:
I wonder how this works - If a Trident Kit with 250x250x250 is needed to build this one why is there 350mm in x and 250mm in x?
Could you explain the calculator in some easy words?
What do i need to change if i want to build one based on a 300x300 Kit?
Will the length of the linear rails also be affected? I guess they should.
Thanks in Advance.

Closed 2023-03-31.

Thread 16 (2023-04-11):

Extrusion

TS-3D, 2023-04-11:
Having problems with extrusion length and speed.
Heating up T0 and T1 225c.
Selecting T0 commands 25mm, speed 2, extruder is ok.

But Selecting T1 commands 25mm, speed 2, extruder pushes 50mm and double speed. Almost starts skipping steps.

Testet svaping mcu addresses, T1 head becomes T0 extrusion is ok.
Something happens in T1 macro i think

TS-3D, 2023-04-19:
Fond the problem [tmc2209 extruder] missing 1

Closed 2023-04-19.

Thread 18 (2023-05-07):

Error in Documentation

ccfman2004, 2023-05-07:
In Part 6 of the documentation for belting the X-Axis you have both Left and Right carriages labeled as T1.

"The X belt routing is similar to a standard CoreXY belt routing, except upper belt attaches to the left X carriage (T1), and the lower belt attaches to the right X carriage (T1)."

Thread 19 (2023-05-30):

Frame Calculator - I wonder how this works

seacred, 2023-05-30:
I wonder how this works - If a Trident Kit with 250x250x250 is needed to build this one why is there 350mm in x and 250mm in y?
Could you explain the calculator in some easy words?
What do i need to change if i want to build one based on a 300x300 Kit?
Will the length of the linear rails also be affected? I guess they should.
Thanks in Advance.

_Originally posted by @seacred in https://github.com/FrankenVoron/Tridex/issues/14#issuecomment-1567299056_

evanvruggink, 2023-06-06:
Because the idle extruder takes space. So to gain this space back, you use 100mm extra width.

Closed 2023-06-12.

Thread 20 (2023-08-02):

Mirrored/Duplication

pasha4ur, 2023-08-02:
Hello

Is there any update for these mods?

There are some kilpper-printers which can print in such modes.

pasha4ur, 2023-08-30:
Looks like author doesn't provide any support.

Here is klipper code for this modes. Maybe somebody can implement it.

https://github.com/Klipper3d/klipper/pull/6297

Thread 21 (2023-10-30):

not getting power to T1 hotend

rlarudqls630, 2023-10-30:
I am almost done with tridex build
However, I cannot get T1 hotend to work.
its not getting enough power.
I know by the fact that can board is getting the power. (24v fans are spinning)
anyone know the reason y this is happening?

joseph-greiner, 2023-10-30:
It could be a bad heater, bad connection, or even some issue with the board. I would recommend reaching out on discord and we can help you troubleshoot there.

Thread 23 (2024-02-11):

Direct access to Tridex_Assembly v13 step file instead of zip file

izanamisu, 2024-02-11:
Hi,

We are using an addon for fusion360 called Voron-Construct ( https://github.com/PrintersForAnts/Voron-Construct)
The addon gives us acces to step files to use in fusion.

The printer files are ziped and are not available in the addon, can you guys unzip and upload the step files to the cad repositories?

eddietheengineer, 2024-02-11:
Hello! The step files are too large to be attached without compression.

On Sun, Feb 11, 2024 at 5:29 AM Marcel Hofstra ***@***.***>
wrote:

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

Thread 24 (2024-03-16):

Motors outside the printing chamber

pasha4ur, 2024-03-16:
Hello @eddietheengineer

Thx for your work.

Can you please make version with motors outside the printing chamber? Like it was in https://github.com/FrankenVoron/IDEX

This will eliminate the need to cool the motors in a heated chamber, and will also make it easier for us to implement such mechanical improvements This will eliminate the need to cool the motors in a heated chamber, and will also make it easier for us to implement such mechanical improvements.

numindast, 2024-09-28:
I highly recommend asking this question in the 'tridex-dev' channel on the doomcube discord. Also try the search function in that channel. There's a link right on the [doomcube github page](https://github.com/FrankenVoron/DoomCube-2).

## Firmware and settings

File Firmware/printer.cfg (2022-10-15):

# This file is an example config file for hybrid corexy style printers also
# known as Markforged kinematic. One may copy and edit this file to configure
# a new hybrid corexy printer.

# DO NOT COPY THIS FILE WITHOUT CAREFULLY READING AND UPDATING IT
# FIRST. Incorrectly configured parameters may cause damage.

# This configuration is with a Spider control board and two Huvud V0.61 CAN toolhead boards

# See docs/Config_Reference.md for a description of parameters.

[include mainsail.cfg]
[include IDEX_mode.cfg]
[include klicky-probe-for_VT.cfg]

[mcu]
serial: /dev/serial/by-id/usb-Klipper_stm32f446xx_200032000851363131363530-if00

[mcu head1]
canbus_uuid: a62a3a4702f5

[mcu head0]
canbus_uuid: cd0403d798dc

[printer]
kinematics: hybrid_corexy
max_velocity: 300
max_accel: 10000
max_accel_to_decel: 10000
max_z_velocity: 10
max_z_accel: 30

#need to be on Klipper Pull Request #5311 to use Input Shaper
#[input_shaper]
#shaper_freq_x: 53
#shaper_type_x: mzv
#shaper_freq_dc: 53 
#shaper_type_dc: mzv
#shaper_freq_y: 40
#shaper_type_y: zv

[adxl345 head0]
cs_pin: head0:PB1
axes_map: y, z, x

[adxl345 head1]
cs_pin: head1:PB1
axes_map: y, z, x

[resonance_tester]
accel_chip: adxl345 head1
probe_points:
    125,125,20  # an example

[force_move]
enable_force_move:true

########################################
# X Steppers
########################################

[stepper_x] 
# Socket X
step_pin: PE11
dir_pin: !PE10
enable_pin: !PE9
microsteps: 32
rotation_distance: 40
endstop_pin: !head0:PA14
position_endstop: -50
position_min: -52
position_max: 228
homing_speed: 60
homing_retract_dist: 5
second_homing_speed: 10

[tmc2209 stepper_x]
# Socket X
uart_pin: PE7
run_current: 0.8
stealthchop_threshold: 0

[dual_carriage]
# Socket Y
axis: x
step_pin: PD8
dir_pin: !PB12
enable_pin: !PD9
microsteps: 32
rotation_distance: 40
endstop_pin: !head1:PA14
position_endstop: 22.4
position_min: 22
position_max: 300
homing_speed: 60
homing_retract_dist: 5
second_homing_speed: 10

[tmc2209 dual_carriage]
# Socket Y
uart_pin: PE15
run_current: 0.8
stealthchop_threshold: 0

########################################
# Y Steppers
########################################

[stepper_y]
# Socket Z
step_pin: PD14
dir_pin: !PD13
enable_pin: !PD15
microsteps: 32
rotation_distance: 40
endstop_pin:  ^PB13
position_endstop: 255
position_max: 255
position_min: -5
homing_speed: 40
homing_retract_dist: 5

[tmc2209 stepper_y]
# Socket Z
uart_pin: PD10
run_current: 0.8
stealthchop_threshold: 0

[stepper_y1]
# Socket E0
step_pin: PD5
dir_pin: PD6
enable_pin: !PD4
microsteps: 32
rotation_distance: 40
endstop_pin: ^PB14 #^PA2 #y-max tmc2209_stepper_y1:virtual_endstop

[tmc2209 stepper_y1]
# Socket E0
uart_pin: PD7
run_current: 0.8
stealthchop_threshold: 0

########################################
# Z Steppers
########################################

[probe]
##	Inductive Probe - Connected to Z MAX
##	This probe is not used for Z height, only Quad Gantry Leveling
##	Connected to Probe Pins
##	If your probe is NO instead of NC, change pin to !PA3
pin: head0:PB12
z_offset: 6.1
x_offset: 0 
y_offset: 21
speed: 5
samples: 3
samples_tolerance: 0.006
samples_result: median
samples_tolerance_retries: 5

[stepper_z]
#Socket E1
step_pin: PE6
dir_pin: PC13
enable_pin: !PE5
microsteps: 32
rotation_distance: 4
endstop_pin: ^PA0
position_endstop: 0.00
position_max: 250
position_min: -3

[tmc2209 stepper_z]
# Socket E1
uart_pin: PC14
run_current: 0.8

[stepper_z1]
#Socket E2
step_pin: PE2
dir_pin: PE4
enable_pin: !PE3
microsteps: 32
rotation_distance: 4

[tmc2209 stepper_z1]
# Socket E2
uart_pin: PC15
run_current: 0.8

[stepper_z2]
#Socket E3
step_pin: PD12
dir_pin: PC4
enable_pin: !PE8
microsteps: 32
rotation_distance: 4

[tmc2209 stepper_z2]
# Socket E3
uart_pin: PA15
run_current: 0.8

########################################
# Extruder 0 (T0) - Left
########################################

[extruder]
step_pin: head0:PB3
dir_pin: head0:PB4
enable_pin: !head0:PB5
heater_pin: head0:PA6 
rotation_distance: 22.8	#Bondtech 5mm Bore Drive Gears
gear_ratio: 50:10 #CW2
full_steps_per_rotation: 200		
microsteps: 16
nozzle_diameter: 0.400
filament_diameter: 1.750
sensor_type: ATC Semitec 104NT-4-R025H42G
sensor_pin: head0:PA0
pullup_resistor: 2200
min_temp: 5
max_temp: 280
pressure_advance: 0.04
pressure_advance_smooth_time: 0.02
#control: pid
max_power: 1.0
#pid_Kp: 26.952
#pid_Ki: 1.321
#pid_Kd: 137.458
max_extrude_only_distance: 220

[tmc2209 extruder]
uart_pin: head0:PA10
tx_pin: head0:PA9
interpolate: False
run_current: 0.5
stealthchop_threshold: 0

[heater_fan extruder_fan]
pin: head0:PA7  # "FAN1"
heater: extruder
heater_temp: 50.0
fan_speed: 1.0

[fan_generic fanX1]
pin: head0:PA8
cycle_time: 0.0100
kick_start_time: 1.00
hardware_pwm: false

########################################
# Extruder1
########################################

[extruder1]
step_pin: head1:PB3
dir_pin: head1:PB4
enable_pin: !head1:PB5
heater_pin: head1:PA6  
rotation_distance: 22.7
gear_ratio: 50:10 #CW2
full_steps_per_rotation: 200
microsteps: 16
nozzle_diameter: 0.400
filament_diameter: 1.750
sensor_type: ATC Semitec 104NT-4-R025H42G
sensor_pin: head1:PA0
pullup_resistor: 2200 
min_temp: 5
max_temp: 280
pressure_advance: 0.04
pressure_advance_smooth_time: 0.02
#control: pid
max_power: 1.0
#pid_Kp: 26.952
#pid_Ki: 1.321
#pid_Kd: 137.458
max_extrude_only_distance: 220

[tmc2209 extruder1]
uart_pin: head1:PA10
tx_pin: head1:PA9
interpolate: False
run_current: 0.5
stealthchop_threshold: 0

[heater_fan extruder1_fan]
pin: head1:PA7   # "FAN1"
heater: extruder1
heater_temp: 50.0
fan_speed: 1.0

[fan_generic fanX2]
pin: head1:PA8
cycle_time: 0.0100
kick_start_time: 1.000
hardware_pwm: false

########################################
# Bed
########################################

[heater_bed]
##	LED-B Output
heater_pin: PB1
sensor_type: Generic 3950
sensor_pin: PC3
##	Adjust Max Power so your heater doesn't warp your bed
##	Target 0.4 W/cm^2
max_power: 1
min_temp: 0
max_temp: 120
pwm_cycle_time: 0.016
#control: pid
#pid_kp: 58.437
#pid_ki: 2.347
#pid_kd: 363.769

########################################
# Sensors and Extras
########################################

[adc_temperature stm32f1_mcu]  # Also valid for stm32f042 mcus
temperature1: 25
voltage1: 1.430
temperature2: 125
voltage2: 1.000 # voltage1 + 100 * -.004300

[temperature_sensor huvud0]
sensor_type: stm32f1_mcu  # Select appropriate mcu sensor type
sensor_pin: head0:ADC_TEMPERATURE
adc_voltage: 3.3
min_temp: 0
max_temp: 120

[temperature_sensor huvud1]
sensor_type: stm32f1_mcu  # Select appropriate mcu sensor type
sensor_pin: head1:ADC_TEMPERATURE
adc_voltage: 3.3
min_temp: 0
max_temp: 120

[temperature_sensor rpi]
sensor_type: temperature_host
gcode_id: D
min_temp: 0
max_temp: 120

[temperature_sensor chamber]
sensor_type: Generic 3950
sensor_pin: head1:PA1
pullup_resistor: 2200
min_temp: -100
max_temp: 100
gcode_id: C

[output_pin caselight]
##	R Channel - PB6
##	G Channel - PB5
##	B Channel - PB7
pin: PB2
pwm: true
cycle_time: 0.01
value: 100
scale: 100
shutdown_value: 100

[neopixel sb_leds_T0]
pin: head0:PA13
#   The pin connected to the neopixel. This parameter must be provided.
chain_count: 3
#   The number of Neopixel chips that are "daisy chained" to the
#   provided pin. The default is 1 (which indicates only a single
#   Neopixel is connected to the pin).
color_order: GRBW
#   Set the pixel order required by the LED hardware. Options are GRB,
#   RGB, GRBW, or RGBW. The default is GRB.
initial_RED: 1
initial_GREEN: 1
initial_BLUE: 1
initial_WHITE: 1.0
#   Sets the initial LED color of the Neopixel. Each value should be
#   between 0.0 and 1.0. The WHITE option is only available on RGBW
#   LEDs. The default for each color is 0.#

[neopixel sb_leds_T1]
pin: head1:PA13
#   The pin connected to the neopixel. This parameter must be provided.
chain_count: 3
#   The number of Neopixel chips that are "daisy chained" to the
#   provided pin. The default is 1 (which indicates only a single
#   Neopixel is connected to the pin).
color_order: GRBW
#   Set the pixel order required by the LED hardware. Options are GRB,
#   RGB, GRBW, or RGBW. The default is GRB.
initial_RED: 1
initial_GREEN: 1
initial_BLUE: 1
initial_WHITE: 1.0
#   Sets the initial LED color of the Neopixel. Each value should be
#   between 0.0 and 1.0. The WHITE option is only available on RGBW
#   LEDs. The default for each color is 0.#

#####################################################################
# 	Displays
#####################################################################


## 	For the mini12864 Display, the [display] and [neopixel] must be uncommented
# mini12864 LCD Display
# connected to exp1/2 on Z(main) MCU
[display]
#	mini12864 LCD Display
lcd_type: uc1701
cs_pin: PC11
a0_pin: PD2
rst_pin: PC10
encoder_pins: ^PC6,^PC7
click_pin: ^!PA8
contrast: 63
#spi_bus: spi1
spi_software_mosi_pin: PA7
spi_software_miso_pin: PA6
spi_software_sclk_pin: PA5
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

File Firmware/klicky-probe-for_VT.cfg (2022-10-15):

# This macro was provided by discord user Garrettwp to whom i give my thanks for sharing it with me.
# I have tweaked it a lot.
#
# this macro is  based on the great Annex magprobe dockable probe macros "#Originally developed by Mental, modified for better use on K-series printers by RyanG and Trails"
# that macro can be found here https://github.com/Annex-Engineering/Annex-Engineering_Other_Printer_Mods/blob/master/All_Printers/Microswitch_Probe/Klipper_Macros/dockable_probe_macros.cfg
#
# by standing on the shoulders of giants, lets see if we can see further

[gcode_macro _User_Variables]
variable_verbose:               True  # Enable verbose output
variable_travel_speed:          200   # how fast all other travel moves will be performed when running these macros
variable_dock_speed:            50    # how fast should the toolhead move when docking the probe for the final movement
variable_release_speed:         75    # how fast should the toolhead move to release the hold of the magnets after docking
variable_z_drop_speed:          20    # how fast the z will lower when moving to the z location to clear the probe
variable_home_z_height:         20    # Z when homing

#bed type
variable_gravity:             'bed'   # What goes down with gravity, bed or gantry?
variable_max_bed_y:             250   # maximum Bed size avoids doing a probe_accuracy outside the bed

# if a separate Z endstop switch is in
# use, specify the coordinates of the switch here (Voron).
# Set to 0 to have the probe move to center of bed
variable_z_endstop_x:            146
variable_z_endstop_y:            254

#dock location 
variable_docklocation_x:        178  # X Dock position
variable_docklocation_y:        252  # Y Dock position
variable_docklocation_z:        -128  # Z dock position (-128 for a gantry mount)
variable_dockarmslenght:        30    # Dock arms lenght, toolhead movement necessary to clear the dock arms

#Umbilical to help untangle the umbilical in difficult situations
variable_umbilical:             False # should we untabgle the umbilical
variable_umbilical_x:           15    # X umbilical position
variable_umbilical_y:           15    # Y umbilical position

# location to park the toolhead
variable_park_toolhead:         True  # Enable toolhead parking
variable_parkposition_x:        125
variable_parkposition_y:        125
variable_parkposition_z:        30

# Do not modify below
gcode:
    {% set Mx = printer['configfile'].config["stepper_x"]["position_max"]|float %}
    {% set My = printer['configfile'].config["stepper_y"]["position_max"]|float %}
    {% set Ox = printer['configfile'].config["probe"]["x_offset"]|float %}
    {% set Oy = printer['configfile'].config["probe"]["y_offset"]|float %}
    {% set Oz = printer['configfile'].config["probe"]["z_offset"]|float %}

    # if docklocation_z is zero, use Home Z height for safety
    {% if docklocation_z == 0 %}
        SET_GCODE_VARIABLE MACRO=_Probe_Variables VARIABLE=docklocation_z VALUE={ home_z_height }
    {% endif %}

    # If x, y coordinates are set for z endstop, assign them
    {% if z_endstop_x != 0 or z_endstop_y != 0 %}
        SET_GCODE_VARIABLE MACRO=_Probe_Variables VARIABLE=z_endstop_x VALUE={ z_endstop_x }
        SET_GCODE_VARIABLE MACRO=_Probe_Variables VARIABLE=z_endstop_y VALUE={ z_endstop_y }

    # if no x, y coordinates for z endstop, assume probe is endstop and move toolhead to center of bed
    {% else %}
        SET_GCODE_VARIABLE MACRO=_Probe_Variables VARIABLE=z_endstop_x VALUE={ (Mx * 0.5) - Ox }
        SET_GCODE_VARIABLE MACRO=_Probe_Variables VARIABLE=z_endstop_y VALUE={ (My * 0.5) - Oy }
    {% endif %}
# This macro was provided by discord user Garrettwp to whom i give my thanks for sharing it with me.
# I have tweaked it a lot.
#
# this macro is  based on the great Annex magprobe dockable probe macros "#Originally developed by Mental, modified for better use on K-series printers by RyanG and Trails"
# that macro can be found here https://github.com/Annex-Engineering/Annex-Engineering_Other_Printer_Mods/blob/master/All_Printers/Microswitch_Probe/Klipper_Macros/dockable_probe_macros.cfg
#
# by standing on the shoulders of giants, lets see if we can see further

[gcode_macro _Probe_Variables]
variable_probe_attached:            False
variable_probe_state:               False
variable_probe_lock:                False
variable_z_endstop_x:               0
variable_z_endstop_y:               0
gcode:


[gcode_macro _exit_point]
gcode:
    {% set function  = 'pre_' ~ params.FUNCTION  %}
    {% set move  = params.MOVE|default(0)  %}
    # mandatory to save the new safe position
    M400
    RESTORE_GCODE_STATE NAME={function} MOVE={move}


[gcode_macro _entry_point]
gcode:
    {% set function  = 'pre_' ~ params.FUNCTION  %}
    # mandatory to save the new safe position
    M400
    SAVE_GCODE_STATE NAME={function}
    # removes the Z offset for better bed based docking
    SET_GCODE_OFFSET Z=0
    # all the macros initially assume absolute positioning
    G90

[gcode_macro _Homing_Variables]
gcode:
    {% set R  = params.RESET|default(0)  %}
    {% if R %}
        SET_GCODE_VARIABLE MACRO=_Probe_Variables VARIABLE=probe_lock VALUE={ False }
    {% endif %}

# Attach probe and lock it
[gcode_macro Attach_Probe_Lock]
description: Attaches Klicky Probe, can only be docked after unlocking
gcode:
    Attach_Probe
    SET_GCODE_VARIABLE MACRO=_Probe_Variables VARIABLE=probe_lock VALUE={ True }

# Dock probe and lock it
[gcode_macro Dock_Probe_Unlock]
description: Docks Klicky Probe even if it was locked
gcode:
    SET_GCODE_VARIABLE MACRO=_Probe_Variables VARIABLE=probe_lock VALUE={ False }
    Dock_Probe

# Unlock Probe
[gcode_macro Probe_Unlock]
description: Unlocks Klicky Probe state
gcode:
    SET_GCODE_VARIABLE MACRO=_Probe_Variables VARIABLE=probe_lock VALUE={ False }

# Lock Probe
[gcode_macro Probe_Lock]
description: Locks Klicky Probe state
gcode:
    SET_GCODE_VARIABLE MACRO=_Probe_Variables VARIABLE=probe_lock VALUE={ True }
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

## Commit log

2021-12-26 Clearance for Stealthburner and Initial Nozzle Scrubber
    [A_Tensioner_Stealth.stl, B_Tensioner_Stealth.stl, Left_Brush_Clamp.stl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]
2022-01-08 Add some CAD files
    [TrideX_Assembly_NozzleBrush v12.f3d]
2022-02-16 Add clearance for inserting screws into skirt
    [front_skirt_a_350_deep.stl, front_skirt_b_350_deep.stl, front_skirt_left.stl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]
2022-09-27 Add CW2 carriages
    [T0_x_carriage_frame_left.stl, T0_x_carriage_frame_right.stl, T1_x_carriage_frame_left.stl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]
2022-10-02 new front idlers and cw2 reorganization
    updated front idler design for better alignment, Gates 20T toothed support, and more
    [A_Tensioner_Stealth.stl, B_Tensioner_Stealth.stl, Huvud_Mount_NEMA17.stl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]
2022-10-02 fix right idler
    [idler_front_right_bottom.stl, idler_front_right_mid.stl, idler_front_right_top.stl]
2022-10-06 fix missing belt opening
    [idler_front_right_top.stl]
2022-10-06 early revision--use at your own risk!
    [[a]_left_drive_mid.stl, [a]_right_drive_mid.stl, drive_left_frame_lower.stl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]
2022-10-06 add locating features to XY joints - USE AT OWN RISK
    [xy_joint_left_lower.stl, xy_joint_left_middle.stl, xy_joint_left_upper.stl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]
2022-10-06 fix chamfer on belt slot
    [xy_joint_left_middle.stl]
2022-10-07 fixes to cutouts and alignment tabs
    [xy_joint_left_middle.stl, xy_joint_left_upper.stl, xy_joint_right_lower.stl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]
2022-10-09 alpha rev wiper update
    [left_wiper_arm.stl, right_wiper_arm.stl, thick_wiper_x2.stl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]
2022-10-09 locate Y idler better, allow clearances for installing without removing MGN9
    [[a]_idler_y_left_tensioner.stl, idler_front_left_bottom.stl, idler_front_right_bottom.stl]
2022-10-10 open clearances for Y endstop, shift 0.5mm forward
    [[a]_left_drive_mid.stl, [a]_right_drive_mid.stl]
2022-10-11 fix belt interference and floating Y idler
    [[a]_idler_y_left_tensioner.stl, idler_front_left_bottom.stl, idler_front_left_top.stl]
2022-10-11 fix bolt overhang feature direction (no reprint needed)
    [idler_front_right_top.stl]
2022-10-12 fix part orientation
    [left_wiper_arm.stl, right_wiper_arm.stl, thick_wiper_x2.stl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]
2022-10-13 add text for identification to idler tensioners
    [[a]_idler_x_left_tensioner.stl, [a]_idler_x_right_tensioner.stl, [a]_idler_y_left_tensioner.stl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]
2022-10-13 REQUIRES SUPPORTS - initial draft parts
    [SB_BMO_Rear_Tridex.stl, SB_Dragon_Rear_Tridex.stl, SB_V6_Rear_Tridex.stl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]
2022-10-13 add logo
    [[a]_left_drive_mid.stl, [a]_right_drive_mid.stl]
2022-10-15 move files and upload firmware config
    [A_Tensioner_Stealth.stl, B_Tensioner_Stealth.stl, Huvud_Mount_NEMA17.stl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]
2022-10-16 upload newer CAD files
    [Tridex_XY_RC_Brush_Blocky v4.step]
2022-10-16 add full CAD assembly
2022-10-19 Add calibration guide
2022-10-23 add panel drawings
    [350x250_bottom.dxf, 350x250_deck.dxf, 350x250_rear.dxf]
2022-10-23 remove old files
    [A_Tensioner_Stealth.stl, B_Tensioner_Stealth.stl, Huvud_Mount_NEMA17.stl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]
2022-11-10 fixed toolhead STL orientation
    [SB_BMO_Rear_Tridex.stl, SB_Dragon_Rear_Tridex.stl, SB_V6_Rear_Tridex.stl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]
2022-11-13 Tweak slight interference
    [idler_front_left_bottom.stl, idler_front_right_bottom.stl]
2022-11-28 Added rear toolhead piece for Revo Voron.
    [SB_Revo_Voron_Rear_Tridex.stl]
2022-12-04 Add frame calculator
